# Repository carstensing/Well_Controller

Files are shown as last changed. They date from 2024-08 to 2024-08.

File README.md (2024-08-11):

# Well Pump Controller <!-- omit from toc -->

This an Arduino project that automates pumping well water for irrigation use.

## Contents <!-- omit from toc -->

- [Description](#description)
- [Components](#components)
- [Objective](#objective)
- [Motivation](#motivation)
- [Obstacles](#obstacles)
    - [Wells Are Inconsistent](#wells-are-inconsistent)
    - [Measuring Flow](#measuring-flow)
- [3D Printed Gauge Head](#3d-printed-gauge-head)
- [Design Negatives](#design-negatives)
    - [Gauge Error](#gauge-error)
    - [Gauge is Short](#gauge-is-short)
    - [High Barrel Inlet](#high-barrel-inlet)
    - [Wet Electronics](#wet-electronics)
- [Design Positives](#design-positives)
    - [Cost](#cost)
    - [Sensor is Arduino Compatible](#sensor-is-arduino-compatible)
    - [Simple](#simple)
    - [Can be Simulated without Water](#can-be-simulated-without-water)
- [Redesign](#redesign)
- [Flow Rate Optimization Algorithm](#flow-rate-optimization-algorithm)

## Description

Utah has been in a drought for many years and irrigation water has been limited
by the city where my grandfather lives. After doing some work in the yard, he
discovered where an old well used to be. He redug the well and discovered that
it still had a good supply of water. He repeated this in a few other spots on
the property and found more water. The wells are about 8-10 feet deep and end
where the water saturates coarse sand. As far as wells go, they are very small
and inexpensive. Nonetheless, this water is free could save his plants over the
hot summer.

To use the well water, he pumps water into small barrels, moves the barrels
around the yard on a wagon and then waters the plants. This is a lot of manual
work in the sun for my grandpa so we want to make the wells work with his
existing irrigation system. For this, water needs to be pumped out
of the wells, stored in a reservoir, and then pumped into the irrigation
system. The end goal is to have the well and irrigation work together
and be fully automated.

## Components

- Well
- Well Pump
- Pipe and Fittings
- 55 Gallon Barrel
- 55 Gallon Barrel Lid with 2" Bung
- [55 Gallon Barrel Level Gauge](https://www.zoro.com/at-a-glance-barrel-level-gauge-55-gal-2-in-npt-b-55-2/i/G3385846/)
- [Arduino UNO WiFi Rev.2](https://store-usa.arduino.cc/products/arduino-uno-wifi-rev2?selectedStore=us)
- [Adafruit VL6180X Time of Flight Distance Ranging Sensor (VL6180)](https://www.adafruit.com/product/3316)
- [STEMMA QT Adapter Cables](https://www.adafruit.com/product/4209)

## Objective

Create a controller for the well pump so that the water reservoir is
automatically filled.

## Motivation

Getting the many gallons needed to irrigate the yard is time consuming and
highly variable due to the nature of the shallow wells. Simpler methods of
controlling the pump have some significant drawbacks that can be remediated
with more the complex logic of a microcontroller.

## Obstacles

### Wells Are Inconsistent

The wells only have so much water that can be pumped at a time. The sand loses
water faster than it can be replenished and eventually it runs dry. Then, some
time is needed for the sand to become saturated again. The run and wait times
differ for each well and change throughout the year. So to automate the
irrigation system, we need to account for and, ideally, optimize these times
intervals. Otherwise, the pump could run dry and/or the irrigation system could
be starved of water. This Arduino project control the pump to solve these
issues.

Inconsistency means that the irrigation system cannot be directly supplied by
the wells. It may take a hours of pumping and waiting to get enough water to
run the irrigation system for ten minutes. Irrigation systems are designed to
run with a constant flow at a consistent pressure, which wouldn't be possible.
This is why a reservoir is needed. With a pump connected to the reservoir, we
can control flow and pressure to mimic water coming from the city. Also, if we
know how much water is in the reservoir, we can make sure that the irrigation
system doesn't use too much at once. We had a 55 gallon drum laying around that
became our reservoir.

### Measuring Flow

When the wells are run by a person, they can see how much water is coming out
of the well and determine when to turn it off as the flow slows. To automate
this system, the Arduino needs to be able to measure this flow rate. With this
information, the software can determine when to turn off the pump and track how
much water has flown into the reservoir.

There are many ways to measure the flow of water. First thought would be to use
a standard water flow meter that gets connected between the pump and the
reservoir, however due to the spurting nature of the well pump it wouldn't read
accurately. Plus they can be hundreds of dollars.

Another thought was to measure the weight of the reservoir barrel. This would
be very accurate but scales that large can be 1-2 thousand dollars. Not only
that, but this limits us to one barrel and takes up more square footage.

## 3D Printed Gauge Head

We ended modifying a barrel level gauge to accommodate a small distance
sensor. This made it possible to digitize the mechanical float gauge so the
Arduino could determine the water level.

**Float gauge**:

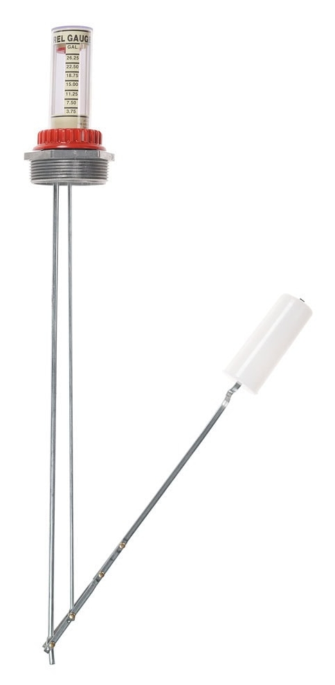
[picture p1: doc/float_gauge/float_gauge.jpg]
Float Gauge


**Gauge head**:

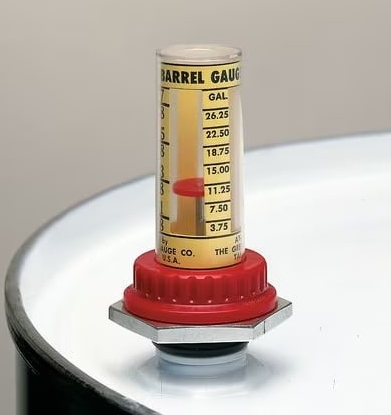
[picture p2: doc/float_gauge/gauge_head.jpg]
Gauge Head


My brother designed and 3D printed a plastic housing that goes around the red
level-indicator. This new housing holds the distance sensory where it can
measure the red disk moving up and down. It was printed clear so that it didn't
lose any existing functionality.

**Printed Housing**:

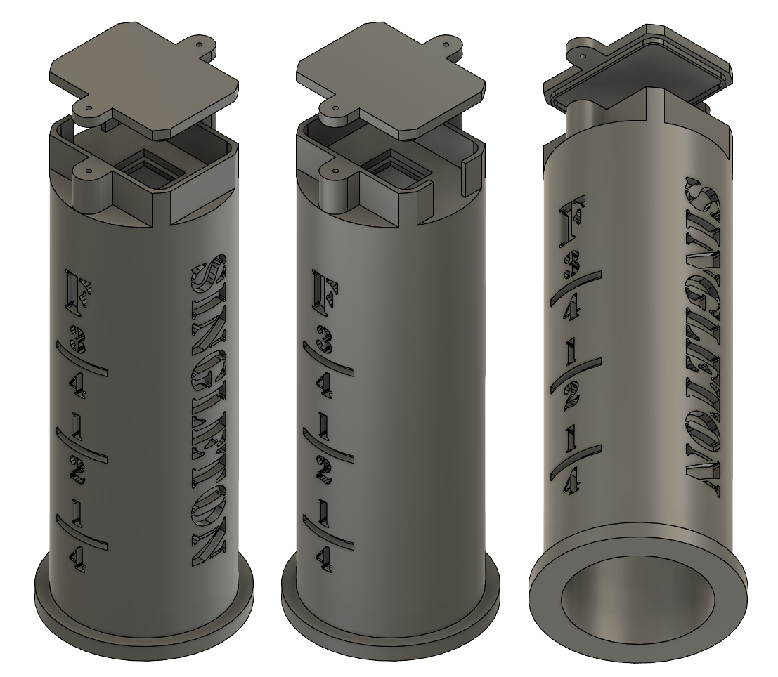
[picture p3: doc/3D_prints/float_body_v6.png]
Float Body


## Design Negatives

### Gauge Error

After we mocked up the system, I realized that measuring the very small
distance that the level gauge moved massively decreases the accuracy of
measuring flow. From zero to full, the gauge moves about 56 mm. That's about a
14x reduction in resolution from a directly measuring the barrel. On top of
that, the gauge easily bobs up and down slightly and introduces error that has
to be accounted for. This error ends up being nearly +/- one gallon, which is a
lot when it comes to water flow out of 3.4" pipe. This makes impossible to
reliably determine small, but meaningful changes in the flow rate.

### Gauge is Short

The lever arm that floats in the barrel needs to be able to swing up and down
without hitting the walls of the barrel. This limits how long the arm can be,
so the float doesn't actually reach the very top or bottom of the barrel.
Essentially making the completely full and empty zones unmeasurable.

### High Barrel Inlet

Well water flows into the barrel from the 3/4" hole in the lid, which creates a
lot of turbulence in the water and introduces more float gauge error.

### Wet Electronics

With the current design, the Arduino and sensor are together atop of the
barrel. This leaves both of them in the potential splash zone and very exposed
to the elements as the barrel will be stored outside.

## Design Positives

### Cost

With the cost of the distance sensor being around $15, it is by far the
cheapest option that we have come up with. This is important because my
grandfather stresses about the project becoming expensive and makes replacing
damaged electronics less concerning.

### Sensor is Arduino Compatible

Using a sensor from Adafruit means that it is plug and play with the Arduino.
We don't have do the work of making some other piece of hardware communicate
with the Arduino somehow. This reduces a lot of potential problems and
headache.

### Simple

After some initial measurements, unit conversions and calculating flow rate
wasn't too complicated.

### Can be Simulated without Water

Using a flow meter or a scale would require using water to get measurements to
the Arduino. This would have made testing and troubleshooting take much longer
and waste a lot of water. With the distance sensor, I can use my hand to test
values.

## Redesign

To fix the issues with the float gauge, I plan on using a 3" pipe with a
floating puck to measure distance. The puck can float all of the way up and
down, and the reading from the sensory will 1:1. The puck can be 3D printed
with an end cap for the pip so it cannot escape. Also, water will fill from the
bottom of the tank to keep the puck from bobbing.

Additionally, I can store the Arduino inside if I use a small communication
board that lives on the barrel with the sensor. This keeps the Arduino safe and
waterproofing smaller components is easier.

## Flow Rate Optimization Algorithm

Since the flow rate accuracy was much lower than expected, I only wrote a simple
well controller. It does the proper conversions and has a simple on/off logic.

My original objective was to write a an algorithm that optimizes the amount of
water per 24 hour period. With some sudo randomness to account for the ever
changing well conditions, this would be pretty simple to do.

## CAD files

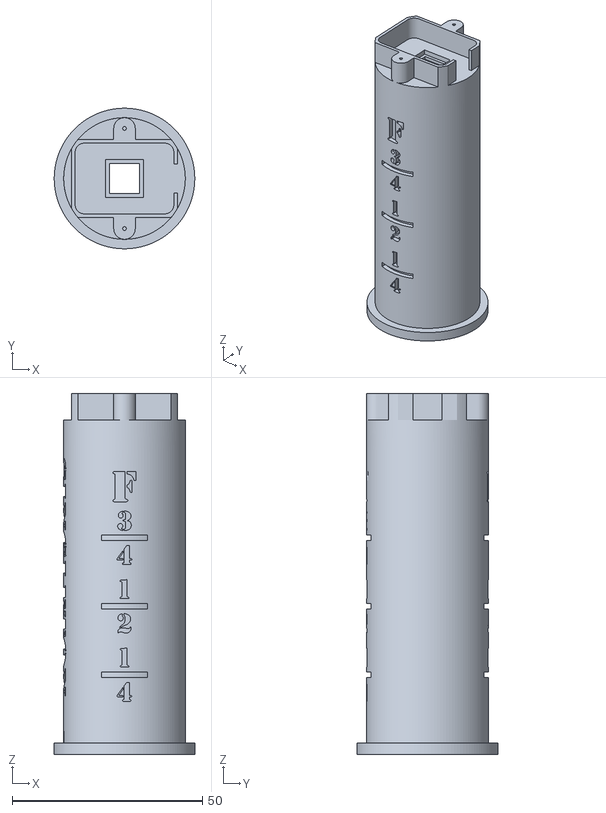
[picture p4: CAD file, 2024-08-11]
3D_print_files/FloatBodyv4.stl
37.0 x 37.0 x 95.0

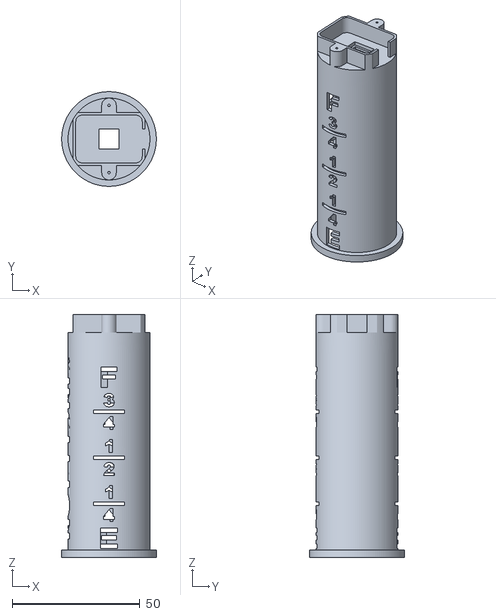
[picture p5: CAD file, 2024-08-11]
3D_print_files/FloatBodyv2.stl
37.0 x 37.0 x 95.0

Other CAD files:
3D_print_files/Float v6.f3d

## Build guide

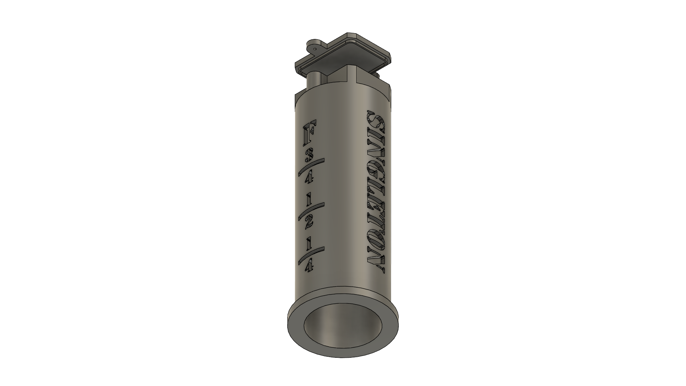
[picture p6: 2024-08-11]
doc/3D_prints/float_body_v6_3.png

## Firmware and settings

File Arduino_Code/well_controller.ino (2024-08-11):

/*
gauge moves ~56 mm
1% = 0.54 mm

Barrel:
1 mm = 16 in^3 = 0.071 gallons
14.08 mm is 1 gallon
float moves 673 mm
1 mm in gauge = 12.46 mm in barrel
1 mm in barrel = 0.08 mm in gauge

best flow is 1 gallon / min

TODO periodic pump turn on to prime pump
*/

#include <Wire.h>
#include <LinkedList.h>
#include "Adafruit_VL6180X.h"

#define MINUTES = 60
#define HOURS = 3600
#define DEFAULT_MIN 16 // distance from sensor to gauge when full
#define DEFAULT_MAX 74 // distance from sensor to gauge when empty
#define PUMP_RELAY 2
#define TICK_TIME 5000000 // seconds in micro seconds
#define NUM_RANGES 24 // number of range data points to collect each TIME_INTERVAL
#define TIME_INTERVAL 24 // in seconds

unsigned long present_time, past_time, time_delta;
unsigned int counter;
unsigned int seconds;
int wait_time;
int time_counter;
float sum_ranges;
float avg_range;
float avg_range_delta;
float percent_full;
bool pump_on;

LinkedList<unsigned int> ranges;

// infrared distance sensor
Adafruit_VL6180X vl = Adafruit_VL6180X();

void setup() {
    Serial.begin(115200);
    Serial.println("VL6180 Start. . .");
    // wait for serial port to open on native usb devices
    while (!Serial) {
        delay(1);
    }

    if (! vl.begin()) {
        Serial.println("Failed to find sensor");
        while (1);
    }
    Serial.println("Sensor found!");

    counter = 0;
    wait_time = 0;
    time_counter = 0;
    sum_ranges = 0;
    // difference between current range and the previous one
    avg_range_delta = 0;
    pump_on = false;

    seconds = 0;
    past_time = micros();
    time_delta = 0;
}

void loop() {
    // float lux = vl.readLux(VL6180X_ALS_GAIN_5);
    // Serial.print("Lux: "); Serial.println(lux);
    
    uint8_t range = 
    .readRange();
    uint8_t status = vl.readRangeStatus();
    present_time = micros();

    // Serial.print("Range: "); Serial.println(range);

    // clock tick tock every second
    time_delta = (present_time - past_time);
    if (time_delta > TICK_TIME) {
        past_time = present_time - (time_delta - TICK_TIME) - 1275;
        seconds++;
        // Serial.println(seconds);

        // average distance inputs and calculate percent full
        if (status == VL6180X_ERROR_NONE) {
            avg_range = float(sum_ranges/counter);
            percent_full = (1.0 - (avg_range-DEFAULT_MIN) / (DEFAULT_MAX-DEFAULT_MIN)) * 100;
            seconds = 0;

            
            if (ranges.size() == NUM_RANGES) {
                avg_range_delta = avg_range - ranges.get(ranges.size() - 1);
                ranges.pop();
            }
            // add average range to the beginning of LinkedList
            ranges.unshift(avg_range);

            Serial.print("Average Range: "); Serial.println(avg_range);
            Serial.print("Range Delta: "); Serial.println(avg_range_delta);
            Serial.print("Percent Full: "); Serial.print(percent_full); Serial.println("%");
            Serial.print("Num Samples: "); Serial.println(counter);
            Serial.print("Wait Time: "); Serial.println(wait_time);
            Serial.print("Pump On: "); Serial.println(pump_on);
        }

        counter = 0;
        sum_ranges = 0;
        if (wait_time > 0) {
            wait_time--;
        }
        if (pump_on) {
            time_counter++;
        }
        
    } else {
        sum_ranges += range;
        counter++;
    }

    // turn pump on and off
    if(pump_on) {
        if (percent_full > 98) {
            digitalWrite(PUMP_RELAY, LOW);
            pump_on = false;

            // if the water level isn't changing much or if the time is up
        } else if (avg_range_delta < 2 || time_counter >= TIME_INTERVAL){
            digitalWrite(PUMP_RELAY, LOW);
            pump_on = false;
            wait_time = 5 * MINUTES; // wait 5 minutes
        }
    } else { //pump off
        if (percent_full < 95 && wait_time <= 0) {
            digitalWrite(PUMP_RELAY, HIGH);
            pump_on = true;
            time_counter = 0;
        }
    }

    // Some error occurred, print it out!
    if (status != 0) {
        if  ((status >= VL6180X_ERROR_SYSERR_1) && (status <= VL6180X_ERROR_SYSERR_5)) {
            Serial.println("System error");
        }
        else if (status == VL6180X_ERROR_ECEFAIL) {
            Serial.println("ECE failure");
        }
        else if (status == VL6180X_ERROR_NOCONVERGE) {
            Serial.println("No convergence");
        }
        else if (status == VL6180X_ERROR_RANGEIGNORE) {
            Serial.println("Ignoring range");
        }
        else if (status == VL6180X_ERROR_SNR) {
            Serial.println("Signal/Noise error");
        }
        else if (status == VL6180X_ERROR_RAWUFLOW) {
            Serial.println("Raw reading underflow");
        }
        else if (status == VL6180X_ERROR_RAWOFLOW) {
            Serial.println("Raw reading overflow");
        }
        else if (status == VL6180X_ERROR_RANGEUFLOW) {
            Serial.println("Range reading underflow");
        }
        else if (status == VL6180X_ERROR_RANGEOFLOW) {
            Serial.println("Range reading overflow");
        } else {
            Serial.println(status);
        }
    }
}
